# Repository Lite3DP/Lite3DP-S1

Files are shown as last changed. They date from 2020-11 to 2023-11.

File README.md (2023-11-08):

# Lite3DP-S1

Copyright 2020 LITE3DP LLC

For additional information, please visit: https://lite3dp.com/download.html

Visit for instructions: https://www.instructables.com/Lite3DP-S1-MSLA-3D-Printer-Arduino-Based-and-Open-/

You can also check out the unaffiliated group: https://github.com/alt-lite3dp

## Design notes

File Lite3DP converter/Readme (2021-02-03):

This software was created to facilitate the process of converting and saving layer images for 3D printing.

It is currently available for Windows and Linux (February 3, 2021 update).

Note for Linux: works with Debian / Ubuntu on desktop computers. Requires the "unzip" command.

As an alternative to this software, the following steps can be carried out:

1) Unzip the ZIP file from Chitubox. This contains numbered PNG images.
2) Use batch image conversion software to convert all PNG images to 24-bit BMP images.
3) Create a folder on the micro SD card and copy all the BMP images there. The name of this folder will appear on the Lite3DP to be selected.

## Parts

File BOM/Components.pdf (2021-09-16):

| Component | Qty. | Example
1 | Arduino Pro Mini, 5V 16MHz (and its CP2102 USB to TTL serial adapter, or an equivalent, to upload the firmware). | 1
2 | Stepper driver DRV8825 | 1
3 | 12V 1A, 5.5x2.1mm plug, power supply. | 1 | Aliexpress (https://www.aliexpress.com/item/4001216578675.html?scm_id=1007.13339.169870.0&scm-url=1007.13339.169870.0)
4 | Linear guide rail MGN7, L=100 mm (or custom length = movement threaded rod length) + MGN7C block. | 1 set
5 | T3.5 movement threaded rod, pitch 1mm, lead 2mm, L=100mm (or custom length = linear guide length); and its POM nut. | 1 | Aliexpress (https://www.aliexpress.com/item/32735839355.html?spm=a2g0s.8937460.0.0.68e42e0e3QXKOS)
6 | Stepper motor: 25mm micro stepper motor with 1:12 reduction. -upgradeable to Nema 8- | 1 | Aliexpress (https://es.aliexpress.com/item/1005001368680827.html?spm=a2g0s.8937460.0.0.22932e0eGFezpk)
7 | Round Screw Ball (10 mm diameter, M4 bore) + Round Magnetic Bracket (12 mm diameter, 4 mm thickness) | 1 set | Aliexpress (https://www.aliexpress.com/item/32590165059.html?spm=a2g0s.9042311.0.0.15424c4dPlXCjF)
8 | PVC hose, 4mm outside diameter and 2mm inside diameter. Cutting length: 15mm. (for the motor coupling) | 1
9 | For PCB: Cylindrical magnets diameter 9 mm, thickness 3 mm | 2
10 | For PCB: Micro SD module, 6 Pin, 18x18 mm | 1 | Aliexpress (https://www.aliexpress.com/item/32885041509.html?spm=a2g0s.9042311.0.0.4af54c4dV3YCQf)
11 | For PCB: LCD TFT 2.2", 14 Pin, ILI9341 driver, 320x240, contrast ratio 500:1, Ref. Tianma TM022HDH26 | 1 | Aliexpress (https://es.aliexpress.com/item/32301385106.html)
12 | For PCB: MR16 Led Driver 12V, 600 mA Output | 1 | Aliexpress (https://www.aliexpress.com/item/32970846657.html?spm=a2g0s.9042311.0.0.4af54c4dV3YCQf)
13 | Heat transfer adhesive tape, to adhere the UV LED to the aluminum base | 1
14 | 3W UV LED, 405 nm, with heatsink "star" aluminum base. | 1
15 | M4 threaded rod, L=24 mm (for platform). | 1
16 | M3 x 8 Allen screws, "button" head | 18
17 | M3 x 18 Allen screws, "button" head | 2
18 | M2 x 6 screws | 7
19 | M3 nuts | 2
20 | M2 nuts | 3
21 | Nylon hexagonal spacer M3, female-female, 35mm length. | 6 | Aliexpress (https://www.aliexpress.com/item/32964425256.html?spm=a2g0s.9042311.0.0.15424c4dPlXCjF)
22 | M3 x 10 screw with knob | 1
23 | M3 x 12 Allen screws, "button" head | 4
24 | FEP film 100x120 mm. | 1
25 | 3D printed parts: "Carriage.STL", "Base.STL", "Support.STL" and "VAT - mod A/B/C.STL" (PLA) | 4
26 | Laser cut metal parts: Base, platform and VAT frame. | 3
27 | Vinyl decals: "Vinyl1.DXF" and "Vinyl2.DXF" | 2

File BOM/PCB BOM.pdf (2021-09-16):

BOM Lite3DP S1 lite3dp.com

Item | Place | Description Qty. | LCSC Part Number Manufacture Part Number Manufacturer Package Product link | Mouser # Mfr. # Manufacturer
8 | PCB | Aluminum Electrolytic Capacitors - Radial, 100uF 25V, 5x11 20% 2LS 2 | C47873 100uF 25V 5*11 CX(Dongguan Chengxing Elec) Radial,5x11mm lcsc.com/product-detail/Aluminum-Electrolytic-Capacitors-Leaded_CX-Dongguan-Chengxing-Elec-100uF-25V-5-11_C47873.html | 647-UVK1E101MDD UVK1E101MDD Nichicon
1 | PCB | Carbon Film Resistor - Through Hole 10 KOhm 5% 1/4W | 2 | C433778 | RD 1/4W 10K J T/B A1 | TyoHM | Axial,2.4x6.5mm | lcsc.com/product-detail/Carbon-Film-Resistors_TyoHM-RD-1-4W-10K-J-T-B-A1_C433778.html | 603-CFR25SJT-52-10K | CFR25SJT-52-10K | Yageo
2 | PCB | Carbon Film Resistor - Through Hole 150 Ohm 5% 1/4W | 1 | C70814 | CFR0W4J0151A50 | UNI-ROYAL(Uniroyal Elec) | Axial | lcsc.com/product-detail/Carbon-Film-Resistors_UNI-ROYAL-Uniroyal-Elec-CFR0W4J0151A50_C70814.html | 603-CFR-25JR-52150R | CFR-25JR-52-150R | Yageo
3 | PCB | Carbon Film Resistor - Through Hole 5 Ohm 5% 1/4W | 1 | C120000 | CF1/4W-5.1Ω±5% T52 | CCO(Chian Chia Elec) | Axial | lcsc.com/product-detail/Carbon-Film-Resistors_CCO-Chian-Chia-Elec-CF1-4W-5-1Ω-5-T52_C120000.html | 603-CFR-25JT-52-5R | CFR-25JT-52-5R | Yageo
4 | PCB | LDO Voltage Regulators 3.3V 1.0A Positive, LD1117A, TO-220 | 1 | C75485 | LD1117AL-33-TA3-A-T | UTC(Unisonic Tech) | TO-220(TO-220-3) | lcsc.com/product-detail/Dropout-Regulators-LDO_UTC-Unisonic-Tech-LD1117AL-33-TA3-A-T_C75485.html | 511-LD1117AV33 | LD1117AV33 | STMicroelectronics
5 | PCB | DC Power Connectors PCB, 5.5 x 2.1MM | 1 | C194407 | DC-470-2.1GP | GANGYUAN | Through Hole | lcsc.com/product-detail/AC-DC-Power-Plugs-Receptacles_GANGYUAN-DC-470-2-1GP_C194407.html | 163-179PH-EX | 163-179PH-EX | Kobiconn
6 | PCB | MOSFET IRLZ44NPBF, TO-220 | 1 | C38774 | IRLZ44NPBF | Infineon Technologies | TO-220(TO-220-3) | lcsc.com/product-detail/MOSFET_Infineon-Technologies-IRLZ44NPBF_C38774.html | 942-IRLZ44NPBF | IRLZ44NPBF | Infineon
7 | PCB | Aluminum Electrolytic Capacitors - Radial, 10uF 25V, 4x7 20% 1.5LS | 1 | C43351 | 10uF 25V 4*7 | CX(Dongguan Chengxing Elec) Radial,4x7mm | lcsc.com/product-detail/Aluminum-Electrolytic-Capacitors-Leaded_CX-Dongguan-Chengxing-Elec-10uF-25V-4-7_C43351.html | 647-USR1E100MDD1TP | USR1E100MDD1TP | Nichicon
9 | PCB | Through Hole Photo Interrupter | 1 | C390039 | DY-ITR8402 | TONYU | Through Hole | lcsc.com/product-detail/Photo-Interrupter_TONYU-DY-ITR8402_C390039.html | 859-LTH-301-05 | LTH-301-05 | Lite-On
10 | PCB | Tactile Switches, Side operation, Round Button, Through Hole, 7.5x6x6.8mm | 4 | C136733 | K2-1102AQ-Q4CW-01 | Korean Hroparts Elec | Through Hole,7.5x6x6.8mm lcsc.com/product-detail/Tactile-Switches_Korean-Hroparts-Elec-K2-1102AQ-Q4CW-01_C136733.html | 611-PTS645VH832 | PTS645VH832LFS | C&K Switches
11 | PCB | Female Header, 8 Pins x 1 Row, Straight, P=2.54mm | 2 | C225505 | A2541HWV-8P | CJT(Changjiang Connectors) | P=2.54mm | lcsc.com/product-detail/Pin-Header-Female-Header_CJT-Changjiang-Connectors-A2541HWV-8P_C225505.html | 992-8FX1L-254MM | 8Fx1L-254mm | Gravitech
12 | PCB | Female Header, 12 Pins x 1 Row, Straight, P=2.54mm | 2 | C225509 | A2541HWV-12P | CJT(Changjiang Connectors) | P=2.54mm | lcsc.com/product-detail/Pin-Header-Female-Header_CJT-Changjiang-Connectors-A2541HWV-12P_C225509.html | 437-3108711201640101 | 310-87-112-01-640101 | Preci-dip
13 | PCB | Male Header, 4 Pins x 1 Row, Straight, P=2.54 mm | 1 | C390680 | 210-91-04GB01 | PINREX | Through Hole | lcsc.com/product-detail/Pin-Header-Female-Header_PINREX-210-91-04GB01_C390680.html | 523-G800W304018EU | G800W304018EU | Amphenol
14 | PCB | Male Header, 2 Pins x 1 Row, Straight, P=2.54 mm | 4 | C390678 | 210-91-02GB01 | PINREX | Through Hole | lcsc.com/product-detail/Pin-Header-Female-Header_PINREX-210-91-02GB01_C390678.html | 649-1012937890201BLF | 10129378-902001BLF | FCI / Amphenol
15 | PCB | Jumper, 2 Pins x 1 Row, Straight, P=2.54 mm | 1 | C5305 | C5305 | BOOMELE(Boom Precision Elec) SIP-2 | lcsc.com/product-detail/Shunts-Jumpers_BOOMELE-Boom-Precision-Elec-C5305_C5305.html | 855-M7582-05 | M7582-05 | Harwin
16 | Stepper motor | Crimping terminal 22~26 RoHS | 4 | C339354 | A2541-TB | CJT(Changjiang Connectors) | - | lcsc.com/product-detail/Terminals_CJT-Changjiang-Connectors-A2541-TB_C339354.html | 571-1-2321921-1 | 1-2321921-1 | TE Connectivity
17 | Stepper motor | Connector Housing, 4 Pins x 1 Row, Straight, P=2.54 mm | 1 | C339332 | A2541H-4P | CJT(Changjiang Connectors) | - | lcsc.com/product-detail/Rectangular-Connectors-Housings_CJT-Changjiang-Connectors-A2541H-4P_C339332.html | 855-M20-1060400 | M20-1060400 | Harwin
18 | Micro SD module | Male Header, 6 Pins x 1 Row, Straight, P=2.54 mm | 1 | C37208 | C37208 | BOOMELE(Boom Precision Elec) 2.54mm 1x6 | lcsc.com/product-detail/Pin-Header-Female-Header_BOOMELE-Boom-Precision-Elec-C37208_C37208.html | 571-826926-6 | 826926-6 | TE Connectivity

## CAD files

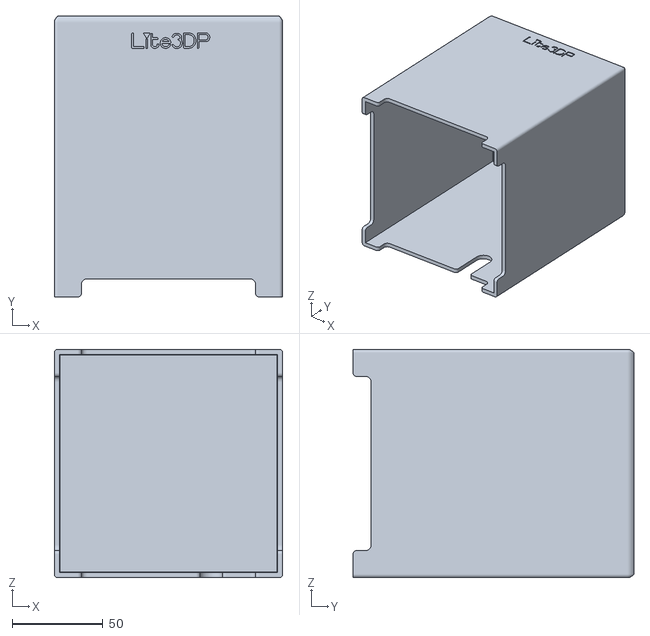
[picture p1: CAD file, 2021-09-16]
STL/Accesories/Acc-FullCover.STL
126.0 x 155.0 x 126.0

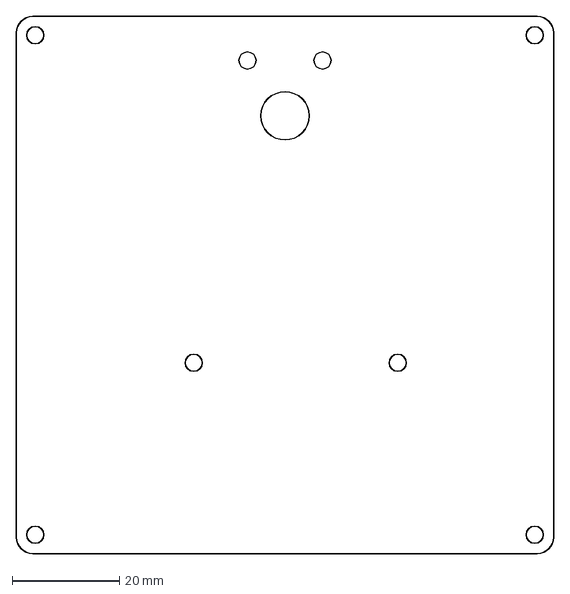
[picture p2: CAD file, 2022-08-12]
DXF - Metal plates/Base - Alu 2mm(v0.2).DXF
100.0 x 100.0 mm

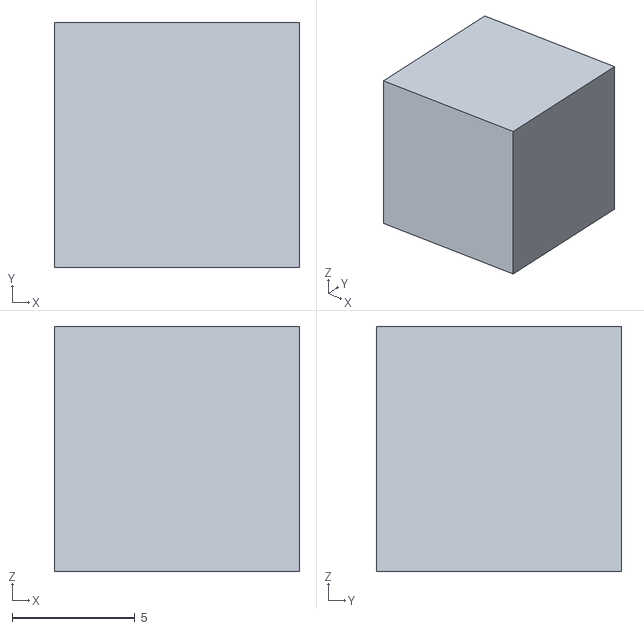
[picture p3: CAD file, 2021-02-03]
SLAcer/stl/cube.center.stl
10.0 x 10.0 x 10.0

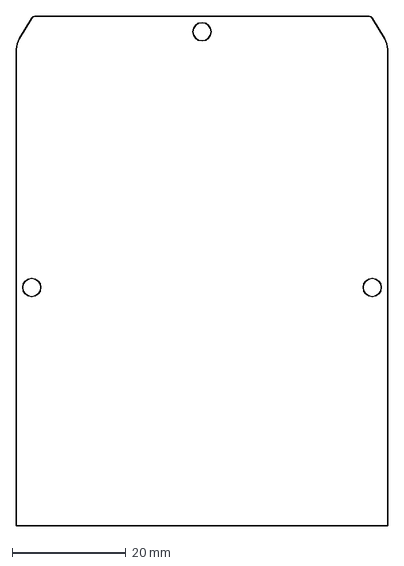
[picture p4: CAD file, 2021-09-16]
STL/Accesories/2mmRedAcrylic-ForCoverModelA.DXF
65.4 x 89.7 mm

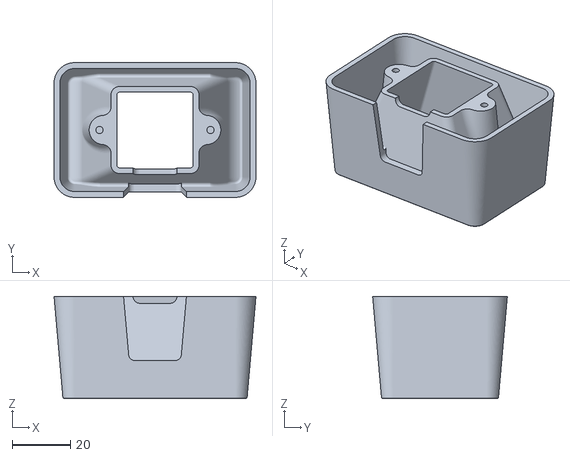
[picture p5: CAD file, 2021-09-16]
STL/Base.STL
69.1 x 46.1 x 35.0

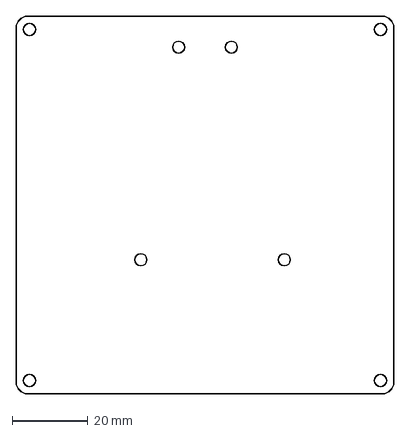
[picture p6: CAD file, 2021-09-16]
DXF - Metal plates/Base - Alu 2mm.DXF
100.0 x 100.0 mm

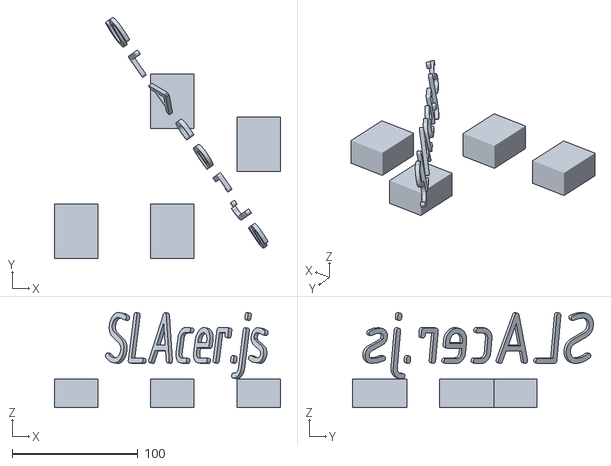
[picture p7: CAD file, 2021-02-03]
SLAcer/stl/SLAcer.stl
179.6 x 191.5 x 75.7

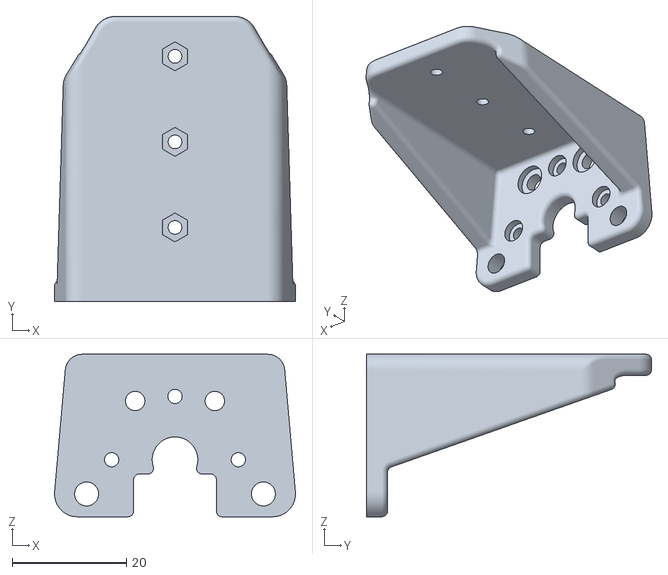
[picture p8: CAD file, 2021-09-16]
STL/Accesories/SupportNema8.STL
42.3 x 50.0 x 28.5

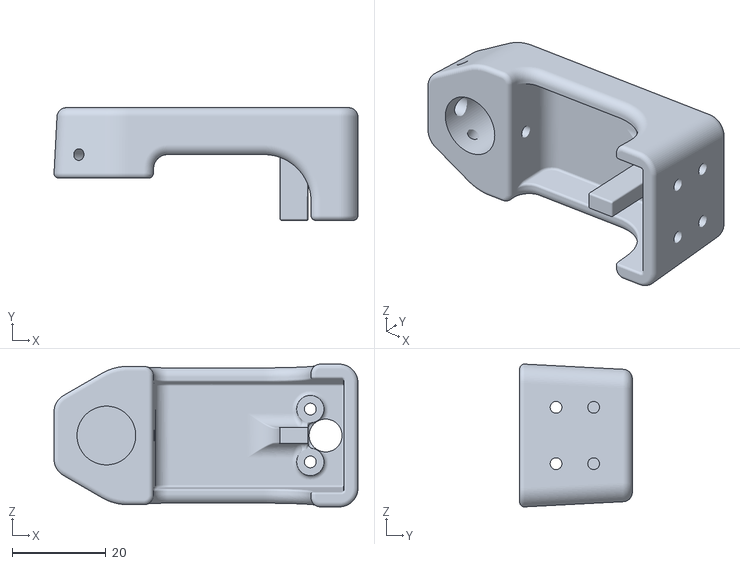
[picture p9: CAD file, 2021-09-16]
STL/Carriage.STL
64.7 x 24.0 x 30.4

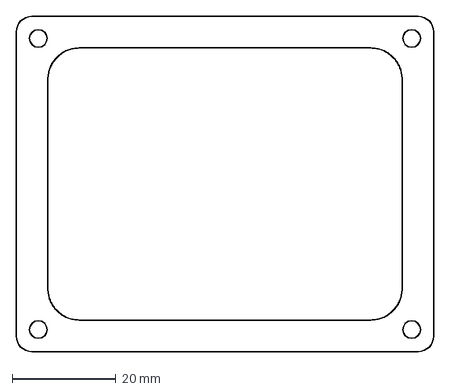
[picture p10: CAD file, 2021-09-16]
DXF - Metal plates/VAT frame - steel 1-8inch.DXF
80.4 x 64.6 mm

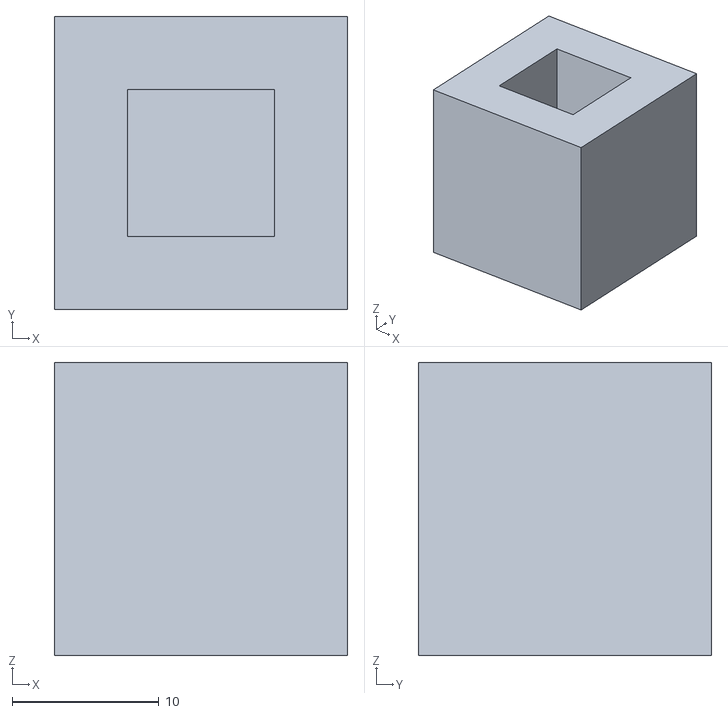
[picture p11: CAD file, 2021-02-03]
SLAcer/stl/cube_hole.stl
20.0 x 20.0 x 20.0

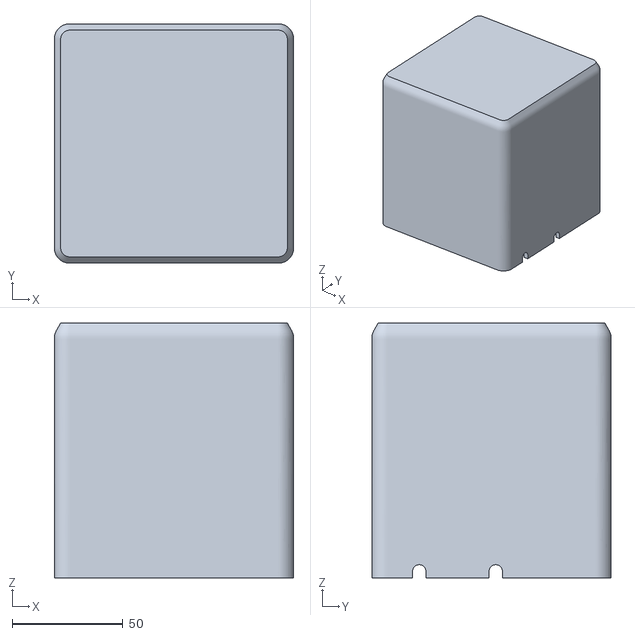
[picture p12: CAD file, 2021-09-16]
STL/Accesories/Acc-Cover-ModelB-Closed.STL
108.0 x 108.0 x 115.0

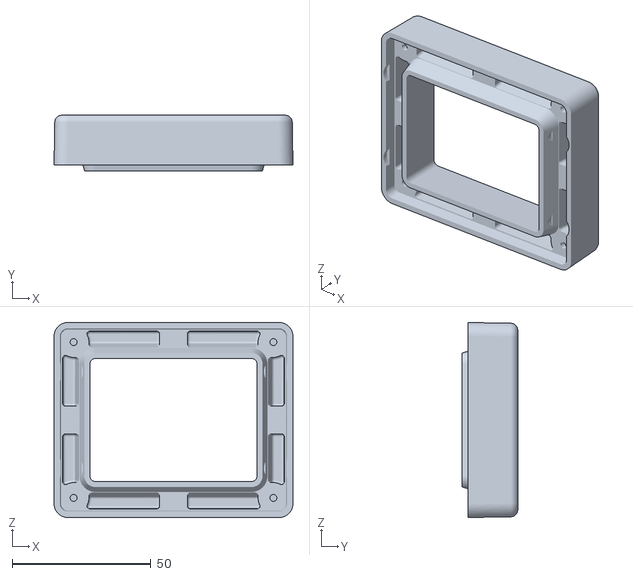
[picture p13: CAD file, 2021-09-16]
STL/VAT - Mod B.STL
86.0 x 20.0 x 70.2

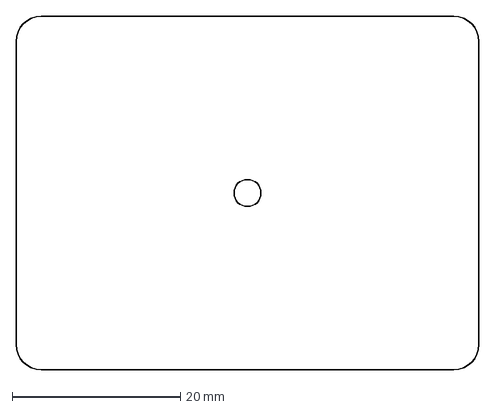
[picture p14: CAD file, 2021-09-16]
DXF - Metal plates/Platform - Alu 3 mm.DXF
55.0 x 42.0 mm

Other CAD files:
SLAcer/stl/StressTest.stl
STL/Accesories/Acc-Base-ModelB-KCD1-11-RockerSwitch.STL
STL/VAT - Mod C.STL
STL/Accesories/Acc-Cover-ModelA.STL
STL/Accesories/Acc-Base-ModelA-NoButton.STL
STL/Support.STL
STL/VAT - Mod A.STL

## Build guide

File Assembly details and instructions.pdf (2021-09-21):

## Lite3DP S1: assembly details and instructions

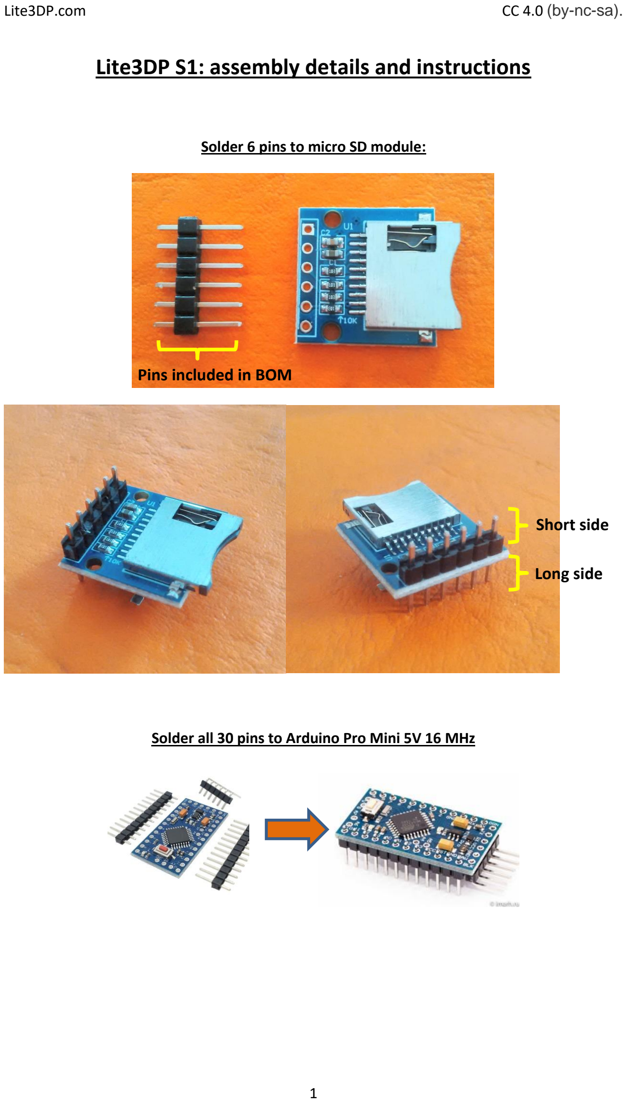
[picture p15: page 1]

Lite3DP.com | CC 4.0 (by-nc-sa).

Solder 6 pins to micro SD module:

Solder all 30 pins to Arduino Pro Mini 5V 16 MHz

Short side

Long side

Pins included in BOM

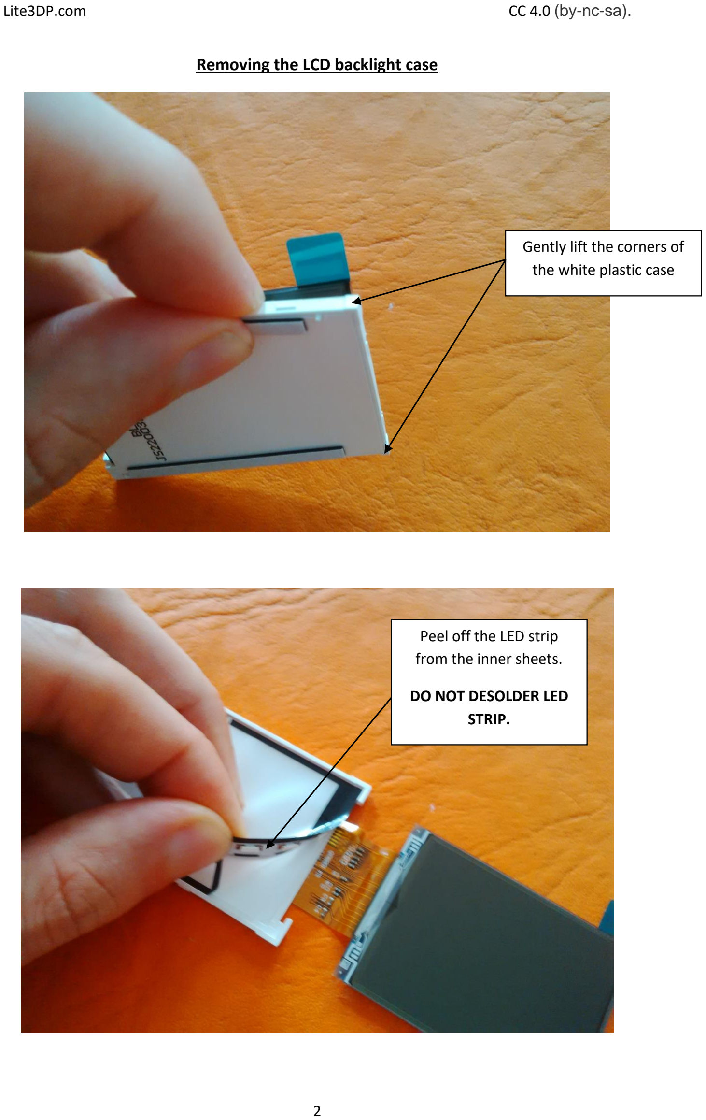
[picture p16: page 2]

Removing the LCD backlight case

Gently lift the corners of the white plastic case

Peel off the LED strip
from the inner sheets.

DO NOT DESOLDER LED
STRIP.

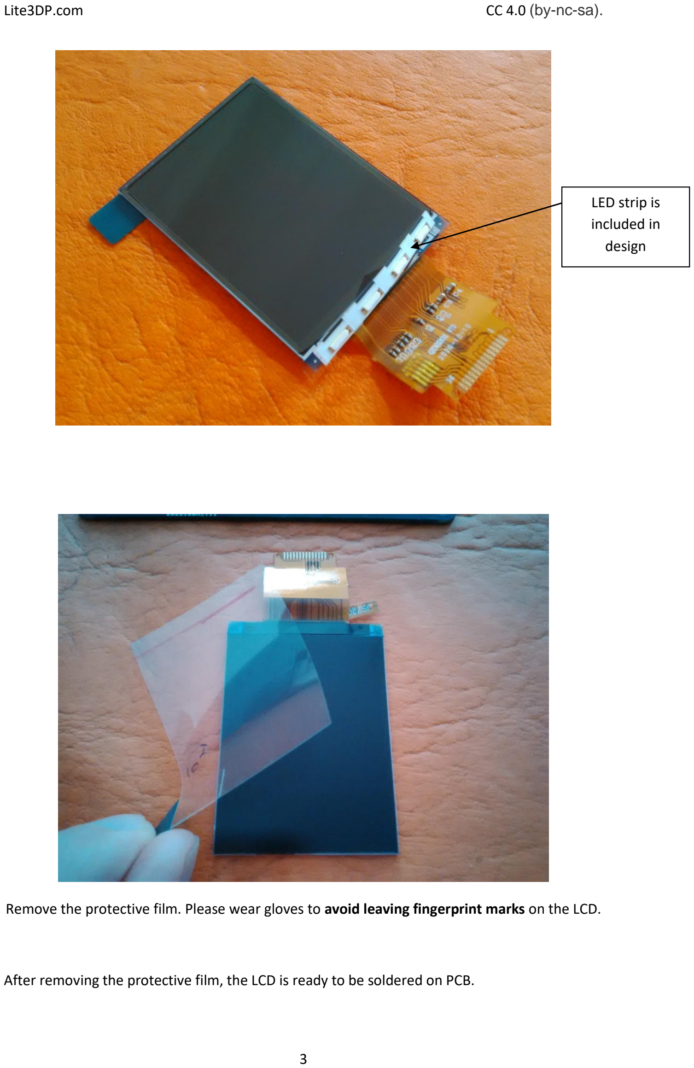
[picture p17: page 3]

Remove the protective film. Please wear gloves to avoid leaving fingerprint marks on the LCD.

After removing the protective film, the LCD is ready to be soldered on PCB.

LED strip is
included in
design

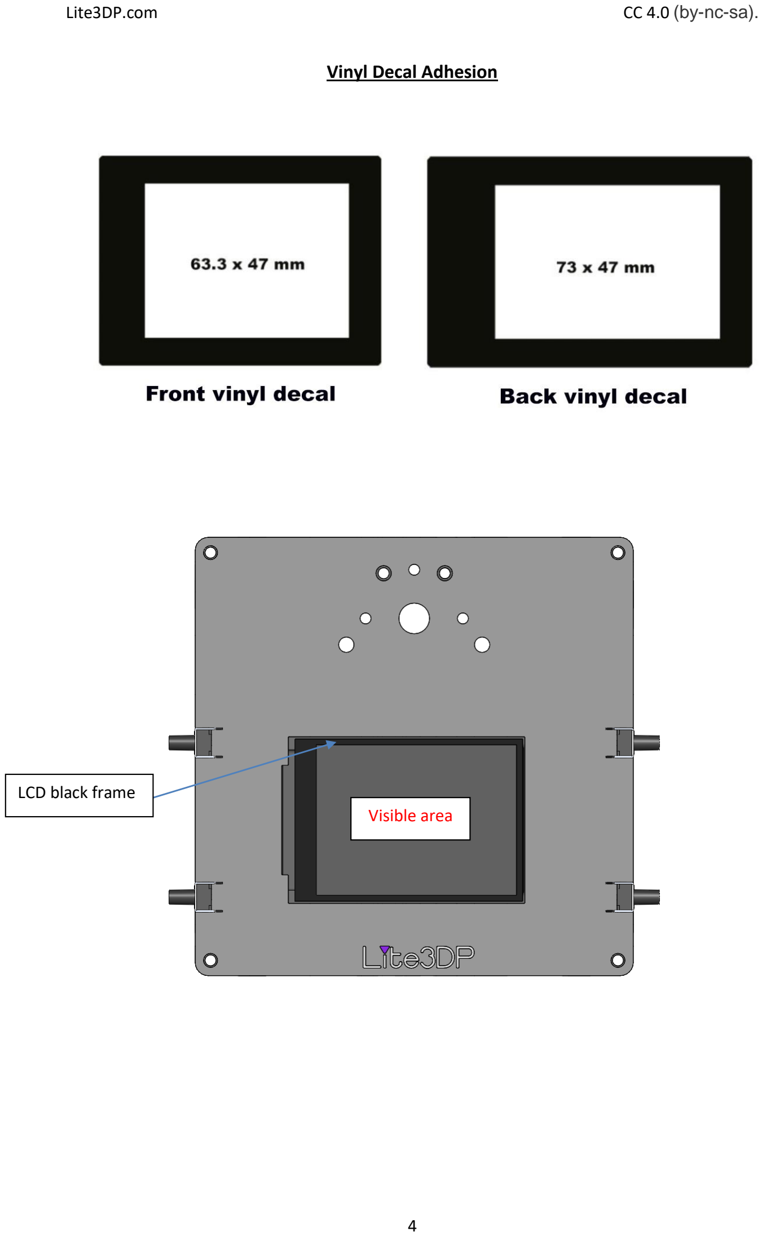
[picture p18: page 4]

Vinyl Decal Adhesion

LCD black frame
Visible area

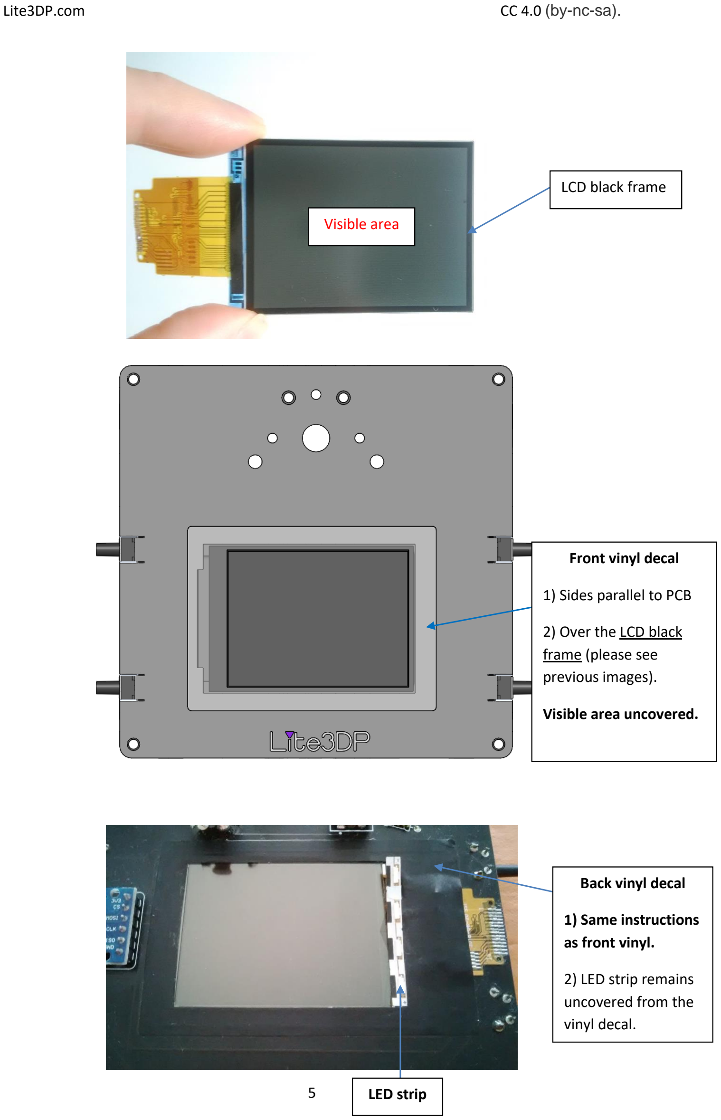
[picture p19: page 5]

Front vinyl decal

1) Sides parallel to PCB
2) Over the LCD black
frame (please see
previous images).

Visible area uncovered.

Back vinyl decal

1) Same instructions
as front vinyl.
2) LED strip remains
uncovered from the
vinyl decal.

LED strip

LCD black frame

Visible area

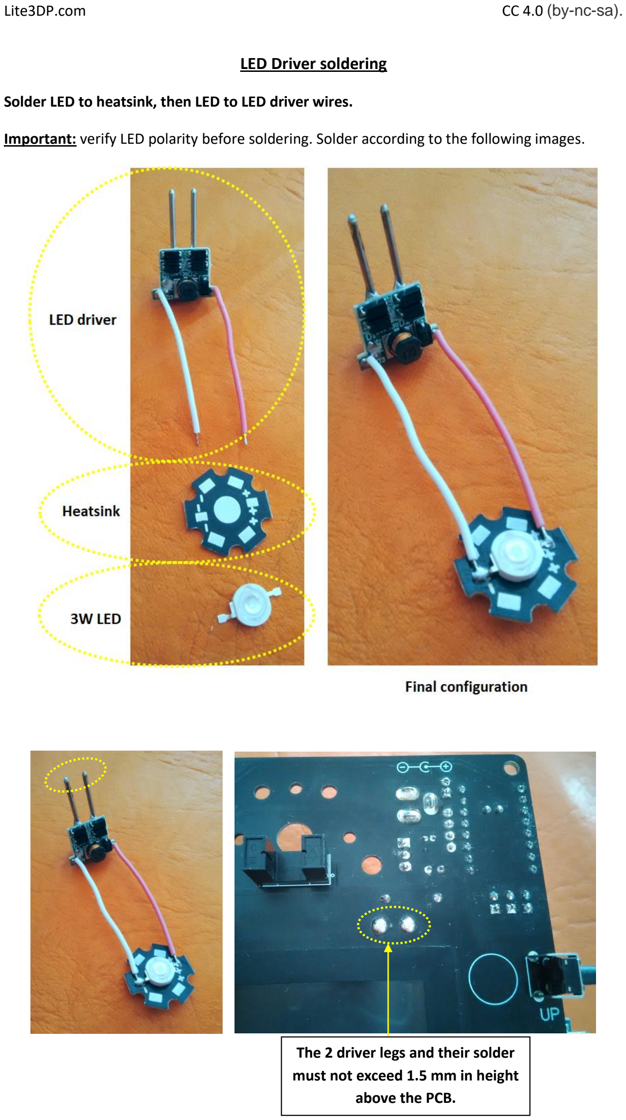
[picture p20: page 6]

LED Driver soldering

Solder LED to heatsink, then LED to LED driver wires.

Important: verify LED polarity before soldering. Solder according to the following images.

The 2 driver legs and their solder must not exceed 1.5 mm in height above the PCB.

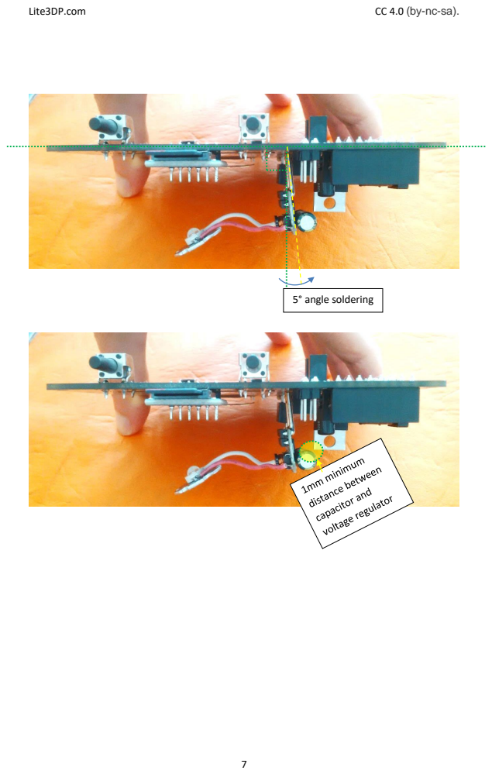
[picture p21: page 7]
5° angle soldering

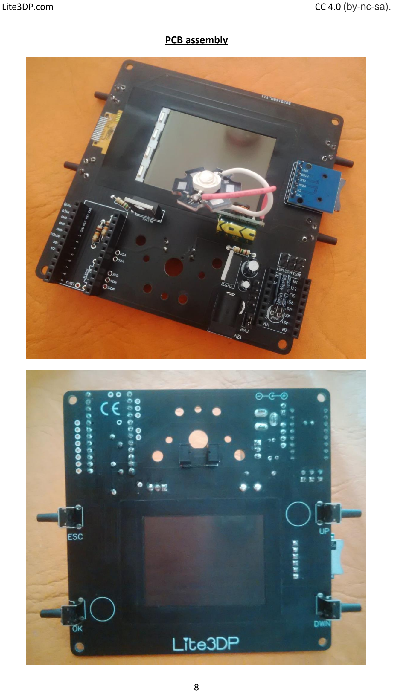
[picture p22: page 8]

PCB assembly

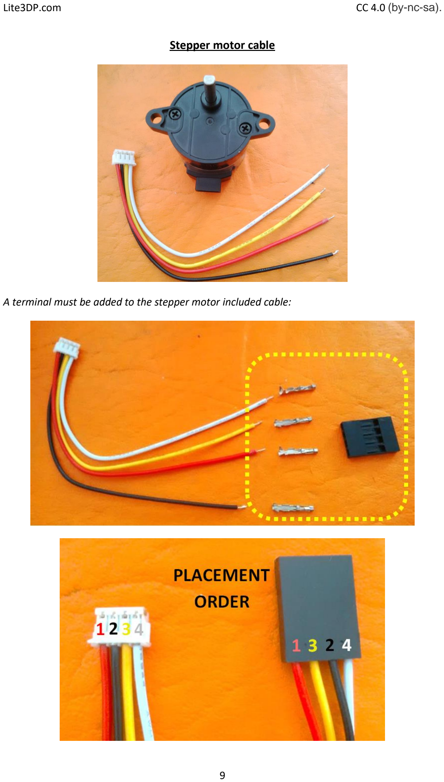
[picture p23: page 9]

Stepper motor cable

A terminal must be added to the stepper motor included cable:

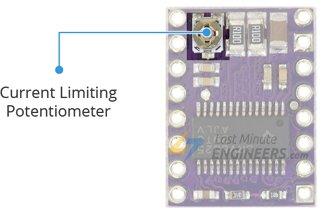
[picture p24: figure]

DRV8825: set limit current + place heatsink

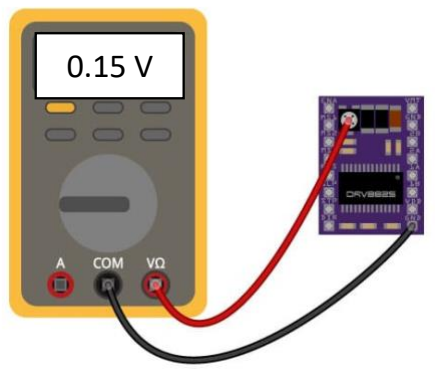
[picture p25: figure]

- Adjust reference Vref to 0,14 – 0,15 V.
- Place heatsink.

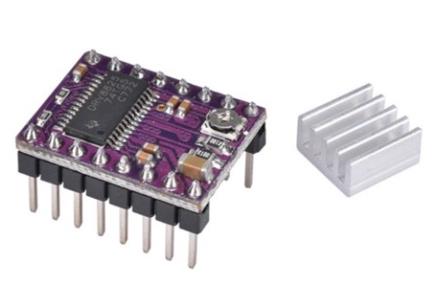
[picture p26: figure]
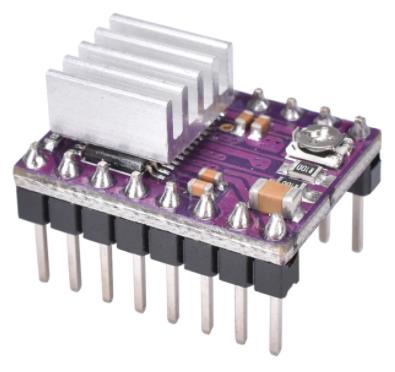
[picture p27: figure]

Libraries installation and firmware upload to Arduino

1) Verify that the computer to be used does not already have a library with one of the following names:

"SdFat"

"Adafruit_GFX_AS"

"Adafruit_ILI9341_AS"

In case you have a library of the same name, please delete it, since another version of the libraries will cause a malfunction.

2) Add the 3 attached libraries, one by one, in the Arduino IDE:

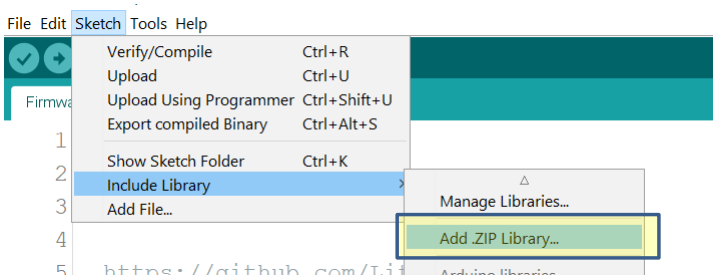
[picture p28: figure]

Libraries to be added:

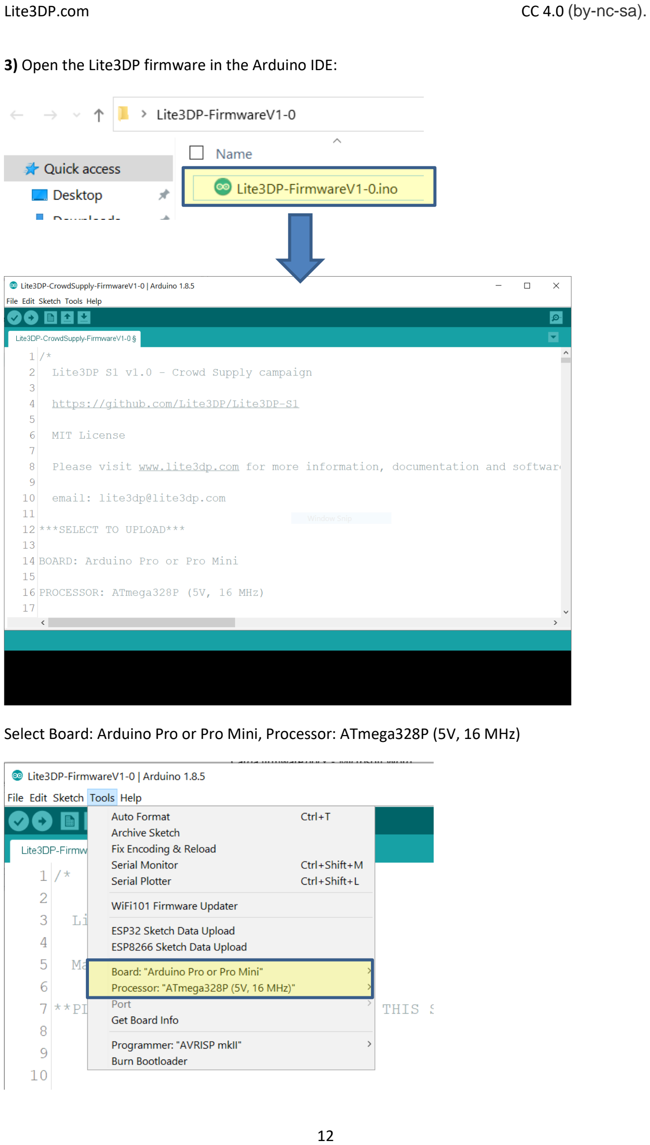
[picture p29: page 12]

3) Open the Lite3DP firmware in the Arduino IDE:

Select Board: Arduino Pro or Pro Mini, Processor: ATmega328P (5V, 16 MHz)

Hit verify/compile and you should get:

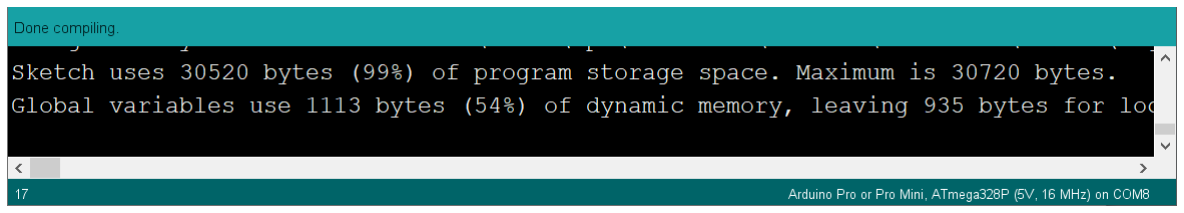
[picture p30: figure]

4) Upload the firmware to Arduino Mini

Connect the Arduino Mini to your CP2102 adapter or similar:

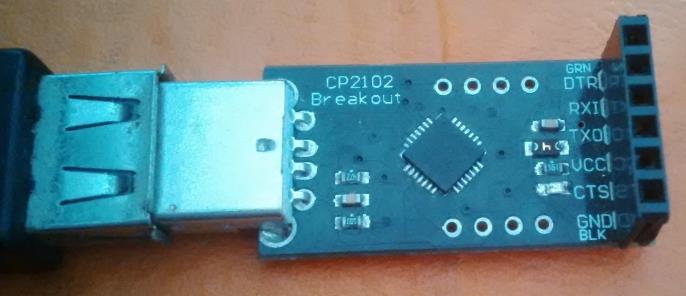
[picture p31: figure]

Select the correct COM port.

Hit Upload until the upload is complete:

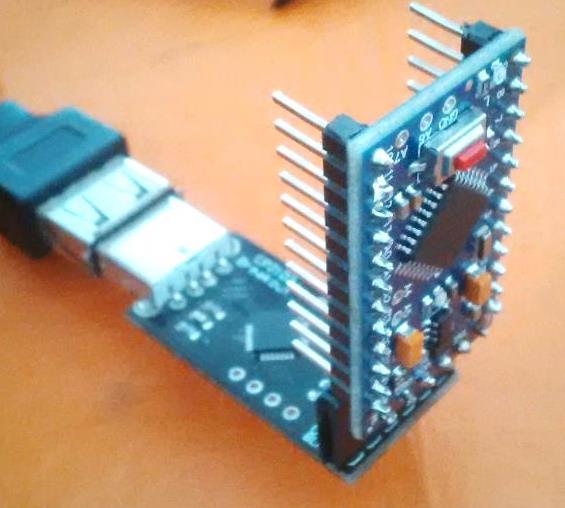
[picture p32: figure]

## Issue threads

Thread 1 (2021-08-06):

Planned macOS Support?

s0urfruit, 2021-08-06:
Hi there,

Is there any planned macOS support?

I plan on backing the S1, but I can't seem to find a build guide for when I get my printer + a macOS version for converter, if not I may make one myself.

Thanks.

eduo, 2021-10-13:
Subscribing to this. It seems the format is straightforward, but rather than a converted it would be nice to know the target files requirements, so a bash script can be made for Mac.

Utopiah, 2021-10-14:
@s0urfruit definitely interested in the add-on board for control via WiFi. For now I keep an eye via a RPi Zero https://twitter.com/utopiah/status/1448388505139306502 but I'd like to keep track of the current status with a webpage or a rest API.

lerouxb, 2021-11-17:
The TL;DR for using imagemagick to convert the png files you get in the zip from chitubox to the right bmp format is to put this in ~/.zshrc or ~/.bashrc and then you can run S1Convert where you extracted the zip:

```bash
function S1Convert() {
    mogrify -format PNG32 *.png
    mogrify -format bmp3 *.PNG32
    for f in *.bmp3; do mv -- "$f" "${f%.bmp3}.bmp"; done
    rm -f *.PNG32 *.png preview_cropping.* preview.* *.gcode
}
```

Copied from the discord here: https://discord.com/channels/902193261316288512/902202128322428928/909160122935291954

Thanks @s0urfruit !

s0urfruit, 2021-12-09:
Just going to close it now.

Closed 2021-12-09.

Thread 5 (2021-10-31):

lead screw nut

mace-man, 2021-10-31:
Please publish the STL file of the lead screw nut.

mace-man, 2021-11-05:
I understand that there is no SLT file.
https://ja.aliexpress.com/item/32735839355.html?spm=a2g0s.8937460.0.0.68e42e0e3QXKOS

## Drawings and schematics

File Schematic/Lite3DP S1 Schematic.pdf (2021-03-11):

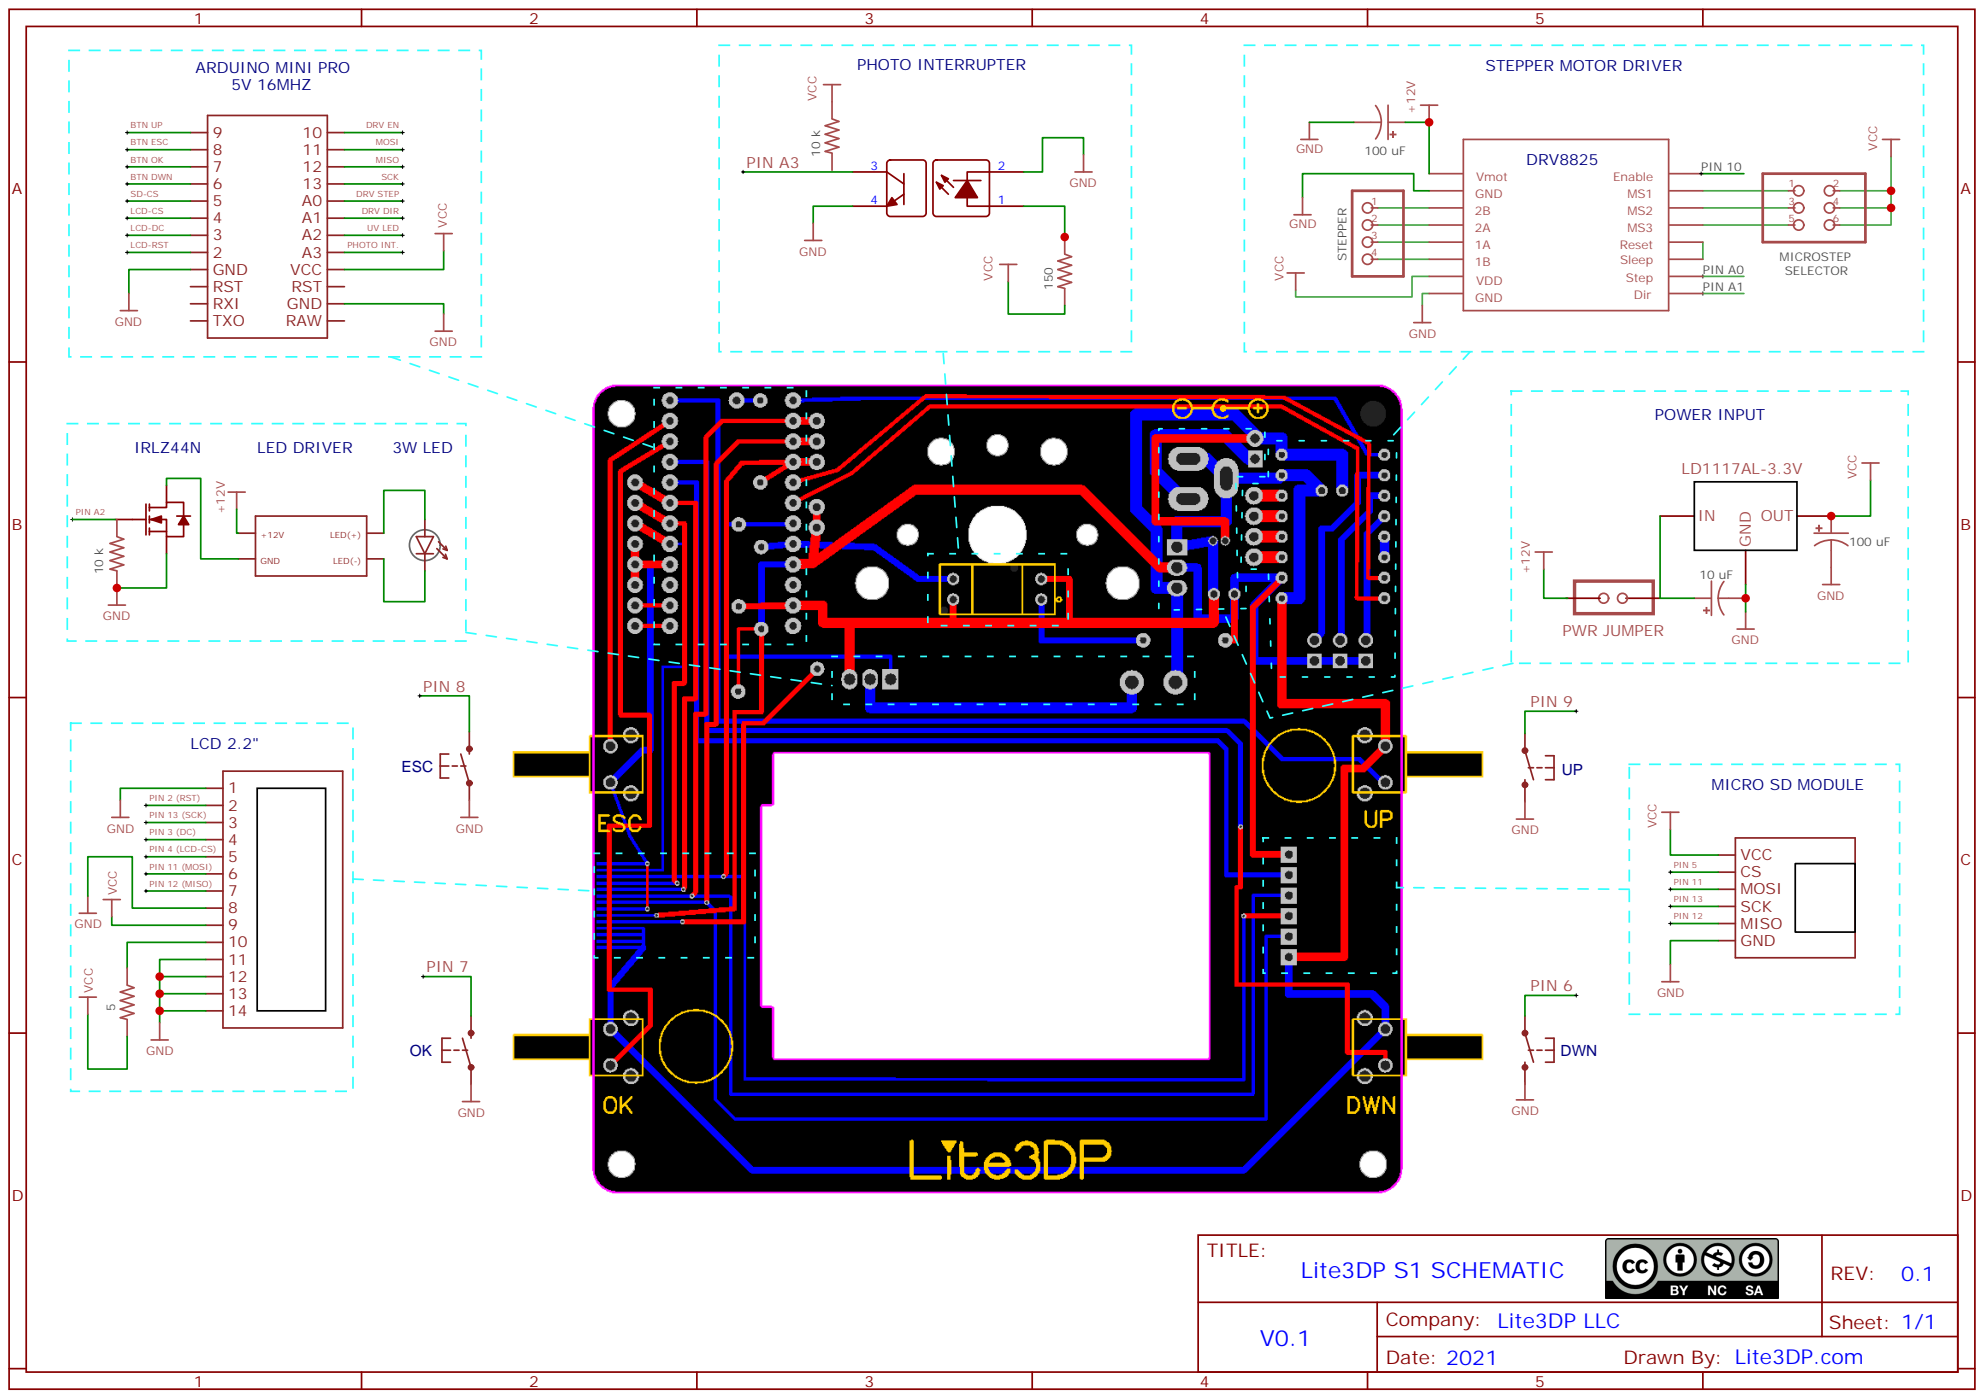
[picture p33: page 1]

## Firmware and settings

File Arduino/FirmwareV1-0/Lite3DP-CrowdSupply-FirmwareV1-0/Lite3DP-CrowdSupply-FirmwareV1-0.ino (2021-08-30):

/*

  Lite3DP S1 v1.0 - Crowd Supply campaign

  https://github.com/Lite3DP/Lite3DP-S1

  MIT License
 
  Please visit www.lite3dp.com for more information, documentation and software.

  email: lite3dp@lite3dp.com

*/


/*
 
***SELECT TO UPLOAD***

BOARD: Arduino Pro or Pro Mini

PROCESSOR: ATmega328P (5V, 16 MHz)

*/


/*
 
  Libraries used:

  SdFat: https://github.com/greiman/SdFat, MIT license

  Adafruit_GFX_AS and Adafruit_ILI9341_AS: https://github.com/Bodmer/TFT_ILI9341 (newest version)

  Original Adafruit library: https://github.com/adafruit/Adafruit_ILI9341

*/


/*

  This is a simple program so that anyone can make changes, upgrades and customizations.

  It is basically structured around a system of numbered "screens" for menu navigation.
  Depending on the screen, the buttons will have different functions. 

  The main functions are "print" and "calibrate".

  The possibility of customizing the motor, the final height and the threaded rod is contemplated ("For customization" section).

  In the configuration section you can change some values such as the lift distance and the number of initial layers.

*/
////////////////////////////////////////////////////////////

// ***** FOR CUSTOMIZATION ****

// If you want to change the length of the linear guide, the threaded rod, the motor or the microsteps
// change them here and the rest of the variables will be updated.


#define Lguide 100               //Total length of linear guide (Default value : 100 mm)

#define pitch 2                  //Pitch of movement screw thread (Default value : 2 mm)

#define stepsMotorPerRev 288     //Motor steps per revolution, including gear reduction (Default value : 288 steps/rev)

#define microsteps 32             //Driver microsteps (Default value 32)


////////////////////////////////////////////////////////////

// **** CONFIGURATION PARAMETERS ****


#define hUp 3                   // Lift distance in mm (Default value: 3 mm)

#define hUpInitial 5            // Inital layers lift distance in mm (Default value: 5 mm)

#define FirstLayers 5           //Number of initial layers (Default value: 5 initial layers)

int expotime = 15;              //Starting exposure time in seconds

int iexpotime = 45;             //Starting initial exposure time in seconds

#define HighSpeed 80          //Delay in microseconds of the stepper motor pulses; higher speed at lower value (Default = 80 microseconds) 

#define LowSpeed 160           //Delay in microseconds of the stepper motor pulses; higher speed at lower value (Default = 160 microseconds)

#define updowntime 6.7          //Printing downtime in seconds. Experimental value used to calculate print times. Counted from turning off the UV light on one layer and turning on the UV light on the next one. 
                                //It must be modified if any of the configuration parameters are changed (speeds, number of initial layers, lift distance).


////////////////////////////////////////////////////////////

// Pin definition

#define PinDir 15
#define PinStep 14
#define PinEn 10

#define sclk 13
#define miso 12
#define mosi 11
#define cs   4
#define dc   3
#define rst  2

#define _sdcs 5

#define BtnUp 9
#define BtnDown 6
#define BtnOK 7
#define BtnCancel 8

#define PinEndStop 17

#define LightPin 16


///////////////////////////////////////////////

// ****LIBRARIES****

#include <Adafruit_GFX_AS.h>
#include <Adafruit_ILI9341_AS.h>
#include <SPI.h>
#include <EEPROM.h>

#include <SdFat.h>
SdFat SD;

Adafruit_ILI9341_AS tft = Adafruit_ILI9341_AS(cs, dc, rst);
#define BU_BMP 1 // Temporarily flip the TFT coords for standard Bottom-Up bit maps
#define TD_BMP 0 // Draw inverted Top-Down bitmaps in standard coord frame


///////////////////////////////////////////////

// ****GLOBAL VARIABLES****

// **Screen number**

byte screen = 1;


//**Button status**

bool edoBtnUP = HIGH;
bool edoBtnDOWN = HIGH;
bool edoBtnOK = HIGH;
bool edoBtnCANCEL = HIGH;


//**Button delay**

#define delaybutton 90


// **EndStop Lecture**

bool LectEndStop;


// **Layer Height**

float hLayer = 0.050;
int hLayerx1000 = hLayer * 1000;


// **Ascendant movement Height (mm)**

int maxheight = Lguide - 30;          //(30 mm lost due to carriage and platform)


// **Print descendant movement**

float hDown = hUp - hLayer;

float hDownInitial = hUpInitial - hLayer;

// **Steps per mm**

int StepsPerMm = stepsMotorPerRev * microsteps / pitch;


// **Calibration aditional steps**

#define maxAddDesc 3     // Additional maximum descent (Default = 3 mm)

int maxAddSteps = maxAddDesc * StepsPerMm / 80;  //Division by 80 is due to memory EEPROM; then it is multiplied again.

int stepsadditional = 0;

int stepsadditionalx80;


// **For the correct name of file**

String DirAndFile;

String FileName;

char *result = malloc(5);

int number;


//**For the layers counter**

int LayersCounter = 0;

int Layers;

String dirfoldersel;


// **For the folder´s name**

File root;

char foldersel[13];

int counter = 1;


///////////////////////////////////////////////



void setup(void) {


  pinMode (BtnUp, INPUT_PULLUP);
  pinMode (BtnDown, INPUT_PULLUP);
  pinMode (BtnCancel, INPUT_PULLUP);
  pinMode (BtnOK, INPUT_PULLUP);

  pinMode (PinDir, OUTPUT);
  pinMode (PinStep, OUTPUT);
  pinMode (PinEn, OUTPUT);

  pinMode (LightPin, OUTPUT);

  pinMode (PinEndStop, INPUT);


  digitalWrite (LightPin, LOW);
  digitalWrite (PinEn, HIGH);

  tft.init();

  screenlite3dp();  //Opening screen

  screen1();   //First menu screen

}


////////////////////////////////////////////////////

void loop() {

  edoBtnUP = digitalRead (BtnUp);
  edoBtnDOWN = digitalRead (BtnDown);
  edoBtnOK = digitalRead (BtnOK);
  edoBtnCANCEL = digitalRead (BtnCancel);

  if (edoBtnUP == LOW) {

    switch (screen) {

      case 1:
        movasc(0.05, HighSpeed);    //Allows the possibility of raising the platform
        break;

      case 11:
        folderUp(root);
        delaybtn();
        break;

      case 12:
        switch (hLayerx1000) {
          case 50:
            hLayer = 0.1;
            hLayerx1000 = hLayer * 1000;
            drawVariableFloat(161, 115, hLayer);
            adjuststeps();
            break;
        }
        delaybtn();
        break;


      case 13:
        if (expotime >= 0 && screen == 13) {
          expotime++;
          tft.fillRect(122, 112, 76, 36, ILI9341_BLACK);
          tft.setTextColor(ILI9341_WHITE);
          drawVariableInt(161, 115, expotime);
        }
        iexpotime = 3 * expotime;   // initial approximation
        delaybtn();
        break;

      case 14:
        if (iexpotime >= 0 && screen == 14) {
          iexpotime++;
          tft.fillRect(122, 112, 76, 36, ILI9341_BLACK);
          tft.setTextColor(ILI9341_WHITE);
          drawVariableInt(161, 115, iexpotime);
        }
        delaybtn();
        break;


      case 21:                                   //screen 21 is when the platform is down during calibration
        if (stepsadditional > 0) {
          stepsadditional--;
          digitalWrite(PinDir, HIGH);
          digitalWrite (PinEn, LOW);
          for (int z = 0; z < 80; z++) {
            edoBtnCANCEL = digitalRead (BtnCancel);
            digitalWrite(PinStep, HIGH);
            digitalWrite(PinStep, LOW);
            delayMicroseconds(LowSpeed);
          }
          digitalWrite (PinEn, HIGH);
        }
        break;

    }

  }

  if (edoBtnDOWN == LOW) {

    switch (screen) {

      case 1:
        break;

      case 11:
        folderDown(root);
        delaybtn();
        break;

      case 12:
        switch (hLayerx1000) {
          case 100:
            hLayer = 0.05;
            hLayerx1000 = hLayer * 1000;
            drawVariableFloat(161, 115, hLayer);
            adjuststeps();
            break;
        }
        delaybtn();
        break;

      case 13:
        if (expotime > 0 && screen == 13) {
          expotime--;
          tft.fillRect(122, 112, 76, 36, ILI9341_BLACK);
          tft.setTextColor(ILI9341_WHITE);
          drawVariableInt(161, 115, expotime);
        }
        iexpotime = 3 * expotime;   // initial approximation
        delaybtn();
        break;

      case 14:
        if (iexpotime > 0 && screen == 14) {
          iexpotime--;
          tft.fillRect(122, 112, 76, 36, ILI9341_BLACK);
          tft.setTextColor(ILI9341_WHITE);
          drawVariableInt(161, 115, iexpotime);
        }
        delaybtn();
        break;

      case 21:                                   //screen 21 is when the platform is down during calibration
        if (stepsadditional <= maxAddSteps) {
          stepsadditional++;
          digitalWrite(PinDir, LOW);
          digitalWrite (PinEn, LOW);
          for (int z = 0; z < 80; z++) {
            edoBtnCANCEL = digitalRead (BtnCancel);
            digitalWrite(PinStep, HIGH);
            digitalWrite(PinStep, LOW);
            delayMicroseconds(LowSpeed);
          }
          digitalWrite (PinEn, HIGH);
        }
        break;

    }

  }


  if (edoBtnOK == LOW) {

    switch (screen) {

      case 1:
        blackscreen();
        calibrate();
        screen = 21;
        break;

      case 11:
        contarlayers();
        if (LayersCounter > maxheight * 20 + 3) {
          cleanscreen();
          tft.drawCentreString("HEIGHT EXCEEDED", 160, 115, 2);
          delay(1200);
          screen = 11;
          screen11();
        }

        else {
          screen = 12;
          screen12();
        }
        break;

      case 12:
        screen = 13;
        screen13();
        break;

      case 13:
        screen = 14;
        screen14();
        break;

      case 14:
        screen = 15;
        screen15();
        break;

      case 15:
        switch (hLayerx1000) {

          case 50:
            Layers = LayersCounter;
            break;

          case 100:
            Layers = LayersCounter / 2;

            int resto = Layers * 2;
            resto = LayersCounter - resto;

            if (resto > 0) {
              Layers++;
            }

            break;
        }

        screen = 16;
        screen16();
        break;

      case 16:
        blackscreen();
        print();
        break;

      case 21:
        EEPROM.write (11, stepsadditional);
        movasc(50, HighSpeed);                    // 50 mm lift to make room for reading the display and tray entry.
        if (!SD.begin(_sdcs, SPI_FULL_SPEED)) {
          digitalWrite (LightPin, LOW);
          cleanscreen();
          tft.drawCentreString("Please", 160, 65, 2);
          tft.drawCentreString("insert SD card", 160, 100, 2);
          screen = 22;
        }
        else {
          digitalWrite (LightPin, LOW);
          root = SD.open("/");
          screen11();
          screen = 11;
        }
        break;

      case 22:
        if (!SD.begin(_sdcs, SPI_FULL_SPEED)) {
          digitalWrite (LightPin, LOW);
          cleanscreen();
          tft.drawCentreString("Please", 160, 65, 2);
          tft.drawCentreString("insert SD card", 160, 100, 2);
          screen = 22;
        }
        else {
          digitalWrite (LightPin, LOW);
          root = SD.open("/");
          screen11();
          screen = 11;
        }
        break;


    }

    delaybtn();

  }

  if (edoBtnCANCEL == LOW) {


    if (screen < 17 && screen > 11 ) {
      screen = 11;
      screen11();
    }

    else {
      screen = 1;
      screen1();
    }
    delaybtn();
  }


}

////////////////////////////////////////////////////////////


//***** MAIN FUNCTIONS *****

// PRINT FUNCTION

void print() {

  number = 1;
  buildfolder();
  calibrate();

  // Printing the first layers (with initial exposure time)

  for (int l = 0; l < FirstLayers; l++) {

    printname();
    digitalWrite (LightPin, HIGH);
    delayprint1();              
    delayprint1();
    delayprint1();
    delayprint1();
    digitalWrite (LightPin, LOW);
    blackscreen();
    pause();                         //allows to enter the pause function by holding down the ESC button
    movasc(hUpInitial, LowSpeed);
    delay(200);
    movdesc(hDownInitial, LowSpeed);

  }

  // Printing the rest

  for (int l = 0; l < Layers - FirstLayers; l++) {

    printname();
    digitalWrite (LightPin, HIGH);
    delayprint2();
    delayprint2();
    delayprint2();
    delayprint2();
    digitalWrite (LightPin, LOW);
    blackscreen();
    pause();                         //allows to enter the pause function by holding down the ESC button
    movasc(hUp, LowSpeed);
    delay(200);
    movdesc(hDown, LowSpeed);

  }

  screen = 17;
  screen17();

}

///////////////////////

// CALIBRATION FUNCTION

void calibrate() {

  LectEndStop = digitalRead(PinEndStop);

  if (LectEndStop != HIGH) {

    desctoendstop();

    delay(600);
    stepsadditional = EEPROM.read(11);
    stepsadditionalx80 = stepsadditional * 80;

    digitalWrite (PinEn, LOW);
    digitalWrite(PinDir, LOW);

    for (int z = 0; z < stepsadditionalx80; z++) {
      edoBtnCANCEL = digitalRead (BtnCancel);
      digitalWrite(PinStep, HIGH);
      digitalWrite(PinStep, LOW);
      delayMicroseconds(LowSpeed);
      if (edoBtnCANCEL == LOW) {
        break;
      }
    }

    digitalWrite (PinEn, HIGH);
  }
}

/////////////////////////////////////////////////////////////

// CALIBRATION AND PRINT SUPPORT FUNCTIONS

void folderDown(File dir) {
  counter++;
  for (int i = 0; i < counter; i++) {
    while (true) {
      File entry =  dir.openNextFile();
      if (! entry) {
        break;
      }
      if (entry.isDirectory()) {
        entry.getName(foldersel, 13);
        break;
      }
      entry.close();
    }
  }
  tft.fillRect(78, 130, 164, 36, ILI9341_BLACK);
  tft.setTextColor(ILI9341_WHITE);
  tft.drawCentreString(foldersel, 161, 134, 2);
  delay(200);

}

void folderUp(File dir) {
  if (counter > 2) {
    counter --;
    for (int i = 0; i < counter; i++) {
      while (true) {
        File entry =  dir.openNextFile();
        if (! entry) {
          break;
        }
        if (entry.isDirectory()) {
          entry.getName(foldersel, 13);
          break;
        }
        entry.close();
      }
    }
    tft.fillRect(78, 130, 164, 36, ILI9341_BLACK);
    tft.setTextColor(ILI9341_WHITE);
    tft.drawCentreString(foldersel, 161, 134, 2);
    delay(200);
  }

}


void movasc (float Mm, int delaysteps) {

  long int stepsmotor = StepsPerMm * Mm;

  digitalWrite (PinEn, LOW);
  digitalWrite(PinDir, HIGH);

  for (long int x = 0; x < stepsmotor; x++) {
    edoBtnCANCEL = digitalRead (BtnCancel);
    digitalWrite(PinStep, HIGH);
    digitalWrite(PinStep, LOW);
    delayMicroseconds(delaysteps);
  }

  digitalWrite (PinEn, HIGH);
}


void movdesc (float Mm, int delaysteps) {

  long int stepsmotor = StepsPerMm * Mm;

  digitalWrite (PinEn, LOW);
  digitalWrite(PinDir, LOW);

  for (long int x = 0; x < stepsmotor; x++) {
    edoBtnCANCEL = digitalRead (BtnCancel);
    digitalWrite(PinStep, HIGH);
    digitalWrite(PinStep, LOW);
    delayMicroseconds(delaysteps);
  }
  digitalWrite (PinEn, HIGH);
}


void buildfolder() {

  DirAndFile = "";
  String folderselString = String(foldersel);
  String barra = "/";
  DirAndFile += barra;
  DirAndFile += folderselString;
  DirAndFile += barra;
  FileName = DirAndFile;

}

void contarlayers() {

  LayersCounter = 0;
  dirfoldersel = "";
  String folderselString2 = String(foldersel);
  number = 1;
  dirfoldersel += "/";
  dirfoldersel += folderselString2;
  dirfoldersel += "/";
  char dirfolderselChar[20];
  dirfoldersel.toCharArray(dirfolderselChar, 20);
  File dircarp = SD.open(dirfolderselChar);
  while (true) {
    File entry =  dircarp.openNextFile();
    if (! entry) {
      break;
    }
    if (entry.isDirectory()) {
    } else {
      LayersCounter ++;
    }
    entry.close();
  }
}


void delayprint1() {
  delay (iexpotime * 250);
}


void delayprint2() {
  delay (expotime * 250);
}


void printname() {
  FileName += number;
  FileName += ".bmp";
  char NameChar[20];
  FileName.toCharArray(NameChar, 20);
  tft.setRotation(3);
  drawBMP(NameChar, 0, 0, BU_BMP);
  switch (hLayerx1000) {
    case 50:
      number ++;
      break;

    case 100:
      number = number + 2;
      break;
  }
  FileName = DirAndFile;
}


void pause() {

  edoBtnOK = digitalRead (BtnOK);
  edoBtnCANCEL = digitalRead (BtnCancel);

  if (edoBtnCANCEL == LOW) {

    float heightActual = number * 0.05;
    float heightAdd = maxheight - heightActual;
    movasc(heightAdd, HighSpeed);
    while (digitalRead (BtnOK) != LOW) {
    }
    movdesc(heightAdd, HighSpeed);
    delaybtn();

  }

}



void desctoendstop() {

  digitalWrite (PinEn, LOW);
  digitalWrite(PinDir, LOW);
  LectEndStop = digitalRead(PinEndStop);

  while (LectEndStop != HIGH) {
    LectEndStop = digitalRead(PinEndStop);
    edoBtnCANCEL = digitalRead (BtnCancel);
    digitalWrite(PinStep, HIGH);
    digitalWrite(PinStep, LOW);
    delayMicroseconds(HighSpeed);
  }
  delay(300);
}


void delaybtn() {
  delay(delaybutton);
}


void adjuststeps() {

  hDown = hUp - hLayer;
  hDownInitial = hUpInitial - hLayer;

}


////////////////////////////////////////////////////////////

// SCREENS


void screenlite3dp() {

  tft.setRotation(3);
  tft.setTextSize(2);
  blackscreen();
  tft.setTextColor(ILI9341_WHITE);
  tft.drawCentreString("Lite3DP", 160, 100, 2);
  tft.fillTriangle(123, 104, 134, 104, 129, 114, ILI9341_BLUE);
  delay(2500);

}


void screen1() {

  tft.setRotation(3);
  cleanscreen();
  bannerpreparation();
  tft.drawCentreString("Prepare!", 160, 120, 2);

}


void screen11() {

  bannerprint();
  cleanscreen();
  tft.setTextColor(ILI9341_WHITE);
  tft.drawCentreString("SELECT FILE", 160, 65, 2);
  tft.drawCentreString(foldersel, 161, 134, 2);
  tft.drawRect(75, 123, 170, 50, ILI9341_WHITE);
  arrows();

}


void screen12() {

  cleanscreen();
  tft.setTextColor(ILI9341_WHITE, ILI9341_BLACK);
  tft.drawCentreString("LAYER HEIGHT", 160, 60, 2);
  drawVariableFloat(161, 115, hLayer);
  tft.drawCentreString("mm", 161, 160, 2);
  rectscreen();
  arrows();

}


void screen13() {

  cleanscreen();
  tft.setTextColor(ILI9341_WHITE);
  tft.drawCentreString("EXPOSURE TIME", 160, 60, 2);
  drawVariableInt(161, 115, expotime);
  tft.drawCentreString("sec", 161, 160, 2);
  rectscreen();
  arrows();

}


void screen14() {

  cleanscreen();
  tft.setTextColor(ILI9341_WHITE);
  tft.drawCentreString("INITIAL EXPOSURE", 160, 60, 2);
  drawVariableInt(161, 115, iexpotime);
  tft.drawCentreString("sec", 161, 160, 2);
  rectscreen();
  arrows();
}


void screen15() {

  cleanscreen();
  tft.setTextColor(ILI9341_WHITE);
  tft.drawCentreString("CONFIRMATION", 160, 55, 2);

  tft.drawString("FOLDER:", 20, 100, 2);
  tft.drawString(foldersel, 220, 100, 2);

  tft.drawString("LAYER H.:", 20, 130, 2);
  drawVariableFloat(250, 130, hLayer);

  tft.drawString("EXP. TIME:", 20, 160, 2);
  drawVariableInt2(220, 160, expotime);

  tft.drawString("INITIAL EXP.:", 20, 190, 2);
  drawVariableInt2(220, 190, iexpotime);

}


void screen16() {

  long int timelayersinitial = FirstLayers * iexpotime;
  long int quantitylayersresto = Layers - FirstLayers;
  long int timerestodelayers = quantitylayersresto * expotime;
  long int timesubebajatot = Layers * updowntime;
  long int timetotalseg = timesubebajatot + timelayersinitial + timerestodelayers;
  long int timetotalmin = timetotalseg / 60;
  int timetotalhours = timetotalmin / 60;
  int restominutes = timetotalmin - timetotalhours * 60;

  tft.setRotation(3);
  blackscreen();
  tft.setTextColor(ILI9341_WHITE);
  bannerprint();

  tft.drawCentreString("DETAILS", 160, 55, 2);

  tft.drawString("TOTAL LAYERS:", 14, 100, 2);
  drawVariableInt2(226, 100, Layers);

  tft.drawString("DURATION:", 14, 135, 2);
  drawVariableInt(175, 135, timetotalhours);
  tft.drawString("h", 195, 135, 2);
  
  drawVariableInt(248, 135, restominutes);
  tft.drawString("min", 272, 135, 2);
  

  tft.drawCentreString("Insert tray and start!", 160, 190, 2);

}


void screen17() {

  tft.setRotation(3);
  blackscreen();

  int heightup = Layers * hLayer;
  int heightremain = maxheight - heightup;

  movasc(heightremain, HighSpeed);

  while (digitalRead (BtnCancel) != LOW) {  //This is for led 13 to blink
    blackscreen();
    delay(100);
  }

}

////////////////////////////////////////////////////////////

// SCREEN SUPPORT FUNCTIONS


void drawVariableInt(int xPos, int yPos, int vartodraw) {
  
String vartodrawString = String(vartodraw);
char vartodrawChar[7];
vartodrawString.toCharArray(vartodrawChar, 7);
tft.drawCentreString(vartodrawChar, xPos, yPos, 2);

}

void drawVariableInt2(int xPos, int yPos, int vartodraw) {
  
String vartodrawString = String(vartodraw);
char vartodrawChar[7];
vartodrawString.toCharArray(vartodrawChar, 7);
tft.drawString(vartodrawChar, xPos, yPos, 2);

}

void drawVariableFloat(int xPos, int yPos, float vartodraw) {
  
String vartodrawString = String(vartodraw);
char vartodrawChar[7];
vartodrawString.toCharArray(vartodrawChar, 7);
tft.drawCentreString(vartodrawChar, xPos, yPos, 2);

}




void arrows() {

  tft.fillTriangle(260, 135, 280, 135, 270, 120, ILI9341_WHITE );  //up arrow
  tft.fillTriangle(260, 165, 280, 165, 270, 180, ILI9341_WHITE );  //down arrow
}


void rectscreen() {

  tft.drawRect(120, 110, 80, 40, ILI9341_WHITE);
}


void blackscreen() {

  tft.fillScreen(ILI9341_BLACK);
}


void cleanscreen() {
  tft.fillRect(0, 40, 320, 200, ILI9341_BLACK);
}



void rectblue () {

  tft.fillRect(0, 0, 320, 40, ILI9341_BLUE);
}



void bannerprint() {

  rectblue();
  tft.setTextColor(ILI9341_WHITE);
  tft.drawCentreString("PRINT", 160, 6, 2);

}


void bannerpreparation() {

  rectblue ();
  tft.setTextColor(ILI9341_WHITE);
  tft.drawCentreString("Lite3DP.com", 160, 6, 2);

}
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

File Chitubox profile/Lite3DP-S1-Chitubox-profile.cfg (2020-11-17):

@@Profile@@__resin:normal
@@Profile@@antiAliasLevel:8
@@Profile@@bAntiAliasLevelEditable:1
@@Profile@@bAntiAliasing:1
@@Profile@@bBottomInnerOutterCircleOffsetEnable:0
@@Profile@@bBuildAreaOffsetEnable:0
@@Profile@@bDisplayCorrectEnable:0
@@Profile@@bImageBlur:0
@@Profile@@bImageBlurPixelEditable:1
@@Profile@@bImageMask:0
@@Profile@@bInnerOutterCircleOffsetEnable:0
@@Profile@@bLockXYSizeRatio:1
@@Profile@@bSurfaceRoughEditable:0
@@Profile@@bottomExposureTimeStrategy:0
@@Profile@@bottomInnerCircleOffset:0
@@Profile@@bottomLayerCount:0
@@Profile@@bottomLayerExposureTime:0
@@Profile@@bottomLayerLiftHeight:0
@@Profile@@bottomLayerLiftHeight2:0
@@Profile@@bottomLayerLiftSpeed:0
@@Profile@@bottomLayerLiftSpeed2:65
@@Profile@@bottomLightIntensityPWM:255
@@Profile@@bottomLightOffTime:0
@@Profile@@bottomOutterCircleOffset:0
@@Profile@@buildAreaOffsetBottom:0
@@Profile@@buildAreaOffsetLeft:0
@@Profile@@buildAreaOffsetRight:0
@@Profile@@buildAreaOffsetTop:0
@@Profile@@circleParityDifference:0
@@Profile@@currProfileName:Profile
@@Profile@@displayCorrectLeftBottomX:0
@@Profile@@displayCorrectLeftBottomY:0
@@Profile@@displayCorrectLeftTopX:0
@@Profile@@displayCorrectLeftTopY:0
@@Profile@@displayCorrectRightBottomX:0
@@Profile@@displayCorrectRightBottomY:0
@@Profile@@displayCorrectRightTopX:0
@@Profile@@displayCorrectRightTopY:0
@@Profile@@edgeCompensationPixel:0
@@Profile@@edgeCompensationTimePercent:100
@@Profile@@endGcode:""
@@Profile@@fillDensity:30
@@Profile@@fillPattern:None
@@Profile@@imageBlurPixel:2
@@Profile@@imageMaskFile:
@@Profile@@innerCircleOffset:0
@@Profile@@layerGcode:""
@@Profile@@layerHeight:0.05
@@Profile@@lightOffTime:0
@@Profile@@machineDepth:33.839999999999996
@@Profile@@machineHeight:70
@@Profile@@machineType:default
@@Profile@@machineWidth:45.12
@@Profile@@maxGreyLevel:255
@@Profile@@minGreyLevel:0
@@Profile@@normalDropDistance2:0
@@Profile@@normalDropSpeed:0
@@Profile@@normalDropSpeed2:150
@@Profile@@normalExposureTime:0
@@Profile@@normalLayerLiftHeight:0
@@Profile@@normalLayerLiftHeight2:0
@@Profile@@normalLayerLiftSpeed:0
@@Profile@@normalLayerLiftSpeed2:65
@@Profile@@normalLightIntensityPWM:255
@@Profile@@outterCircleOffset:0
@@Profile@@projectType:LCD_mirror
@@Profile@@resetTimeAfterLift:0
@@Profile@@resetTimeBeforeLift:0
@@Profile@@resinDensity:1
@@Profile@@resinPrice:1
@@Profile@@resinUnit:$/L
@@Profile@@resolutionX:320
@@Profile@@resolutionY:240
@@Profile@@shellThickness:1
@@Profile@@startGcode:"\n"
@@Profile@@surfaceRoughLevel:1
@@Profile@@zSlowUpDistance:0
__resin:normal
antiAliasLevel:8
bAntiAliasLevelEditable:1
bAntiAliasing:1
bBottomInnerOutterCircleOffsetEnable:0
bBuildAreaOffsetEnable:0
bDisplayCorrectEnable:0
bImageBlur:0
bImageBlurPixelEditable:1
bImageMask:0
bInnerOutterCircleOffsetEnable:0
bLockXYSizeRatio:1
bSurfaceRoughEditable:0
bottomExposureTimeStrategy:0
bottomInnerCircleOffset:0
bottomLayerCount:0
bottomLayerExposureTime:0
bottomLayerLiftHeight:0
bottomLayerLiftHeight2:0
bottomLayerLiftSpeed:0
bottomLayerLiftSpeed2:65
bottomLightIntensityPWM:255
bottomLightOffTime:0
bottomOutterCircleOffset:0
buildAreaOffsetBottom:0
buildAreaOffsetLeft:0
buildAreaOffsetRight:0
buildAreaOffsetTop:0
circleParityDifference:0
currProfile:Profile
displayCorrectLeftBottomX:0
displayCorrectLeftBottomY:0
displayCorrectLeftTopX:0
displayCorrectLeftTopY:0
displayCorrectRightBottomX:0
displayCorrectRightBottomY:0
displayCorrectRightTopX:0
displayCorrectRightTopY:0
edgeCompensationPixel:0
edgeCompensationTimePercent:100
endGcode:""
fillDensity:30
fillPattern:None
imageBlurPixel:2
imageMaskFile:
innerCircleOffset:0
layerGcode:""
layerHeight:0.05
lightOffTime:0
machineDepth:33.839999999999996
machineHeight:70
machineType:default
machineWidth:45.12
maxGreyLevel:255
minGreyLevel:0
normalDropDistance2:0
normalDropSpeed:0
normalDropSpeed2:150
normalExposureTime:0
normalLayerLiftHeight:0
normalLayerLiftHeight2:0
normalLayerLiftSpeed:0
normalLayerLiftSpeed2:65
normalLightIntensityPWM:255
outterCircleOffset:0
projectType:LCD_mirror
resetTimeAfterLift:0
resetTimeBeforeLift:0
resinDensity:1
resinPrice:1
resinUnit:$/L
resolutionX:320
resolutionY:240
shellThickness:1
startGcode:"\n"
surfaceRoughLevel:1
zSlowUpDistance:0

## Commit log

2020-10-01 Create Arduino Firmware
2022-08-12 12-8-2022 update: Compatible with "Zero" model.
    [Base - Alu 2mm(v0.2).DXF]
